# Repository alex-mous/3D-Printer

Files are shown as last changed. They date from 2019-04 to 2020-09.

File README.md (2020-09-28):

<h2> New 3D Printer </h2>

<h3> Introduction </h3>
<h4> Background </h4>
In 2016, I built an Anet A8 budget 3D printer from a kit. During two years of use, the following
issues became evident: <br>
• Print quality (surface quality and amount of ringing) rapidly degraded with an increase in
print speed <br>
• A lack in frame sturdiness caused low quality parts from shaking
induced by the moving axes <br>
• Bolts loosened with use causing rapid degradation in calibration,
giving rise to repeated long setup times <br>
• The heat bed was underpowered and could not heat up quickly or
reach temperatures above 95℃ (required to print certain plastics) <br>
• Print volume was limited to 220x220x230mm

<h4> Engineering Goal </h4>
The goal of this project is to design and build and improved, easy to run, budget 3D printer costing less than $750 for home users to create high quality, high speed prints with a minimum print volume of 275x275x325mm (2.475x10<sup>7</sup>mm<sup>3</sup>).

<h4> Criteria and Constraints </h4>
• Parts and materials must cost less than $750 <br>
• At a print speed of 60mm/s, ringing must be less than a 3 on a ringing scale of 1-6 (1 is negligible, 6 is significant) and roughness must be less than a 3 on a roughness scale of 1-6 (1 is smooth, 6 is rough) <br>
• Print tolerance of ±0.2mm on a 25mm cube <br>
• A minimum print volume of 275x275x325mm (2.475x107mm3) <br>
• Sturdy frame and design <br>
• Powerful heat bed capable of quickly heating to more than 110℃ <br>

<h4> Test Plan </h4>
The following tests were printed on both the Anet A8 and the new printer. The test prints were
then compared and analyzed. <br>
1. Calibration cubes (25x25x25mm) at print speeds from 30-80mm/s in 10mm/s steps with an
acceleration of 1250mm/s2 testing for: <br>
&nbsp&nbsp&nbsp&nbspa. Ringing <br>
&nbsp&nbsp&nbsp&nbspb. Surface quality <br>
&nbsp&nbsp&nbsp&nbspc. Tolerance <br>
2. #3DBenchys to test the ability to print difficult features (such as overhangs, bridges, complex
rounded shapes, etc.) <br>
3. Paper Basket Torture Tests to verify the maximum practical print volumes and identify any
additional common printing issues  <br>

<h4> Results/Conclusion </h4>
<table>
  <tr> <th>Critera and Constraints</th> <th>Result</th> </tr>
  <tr> <td>Parts and materials must cost less than $750</td> <td>✓</td> </tr>
  <tr> <td>At a print speed of 60mm/s, ringing must be less than a 3 on a
ringing scale of 1-6 (1 is negligible, 6 is significant) and roughness
must be less than a 3 on a roughness scale of 1-6 (1 is smooth, 6
is rough)</td> <td>✓</td> </tr>
  <tr> <td>Print tolerance of ±0.2mm on a 25mm cube</td> <td>✓</td> </tr>
  <tr> <td>A minimum print volume of 275x275x325mm (2.475x10<sup>7</sup>mm<sup>3</sup>)</td> <td>4% less than
theoretical due to V3 of Hotend Carriage</td> </tr>
  <tr> <td>Sturdy frame and design</td> <td>✓</td> </tr>
  <tr> <td>Powerful heat bed capable of quickly heating to more than 110℃</td> <td>✓</td></tr>
</table>

<h3>
Warning! This project involves AC wiring and temperatures in excess of 200&degC. Proceed only if you are sure that you know what you are doing!
</h3>

<h3> BOM and Cost </h3>
See BOM.pdf for a list of the parts that need to be purchased. The total cost is around $725. However, your actual cost may vary depending on shipping, tax, etc. Note: the two rolls of PLA filament quoted are an estimate of how much plastic was used. You may find that you need more filament. Also, while you may be able to find cheaper alternatives to some of these parts, please be careful when economizing on very important parts such as the hotend. Some parts may need modification to work properly.

<h3> Tools </h3>
A list of the tooling required is in Tooling.pdf. Please tell me if you find you need more tools so I can add those tools to the list.

<h3> 3D Printed Parts </h3>
The STL files for the 3D printed parts are in the STL files folder. See Printed Parts.pdf for the amount of each part that needs to be printed. Note: some designs may need small modifications after printing such as enlarging holes. Some of these modifications are listed in the Printed Part.pdf file. Please notify me of any modifications made to the parts so that I can update the design files.

<h3> Assembly </h3>
<h4> Step 1: Aluminum Frame </h4>
First, print some of the M6 spacers (see Printed Parts.pdf). Next, prepare an aluminum L-bracket as shown below with two T-slot nuts, two M6x20 screws and two spacers. Repeat this for 28 of the L-brackets.

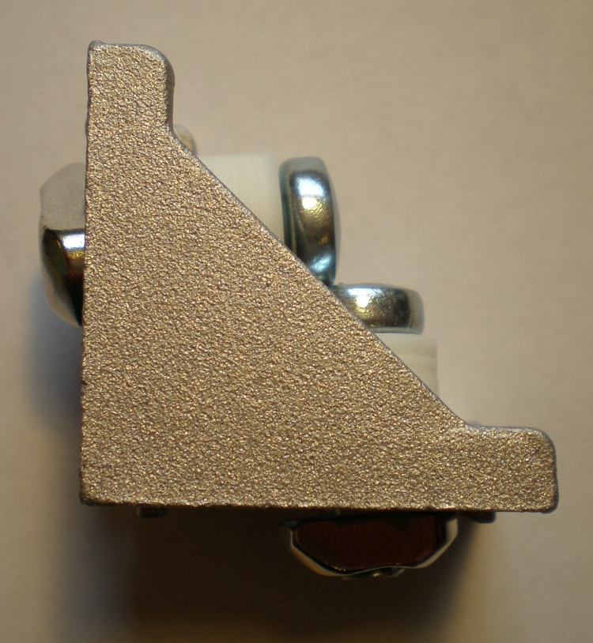
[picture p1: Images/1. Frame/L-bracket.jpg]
Side of bracket
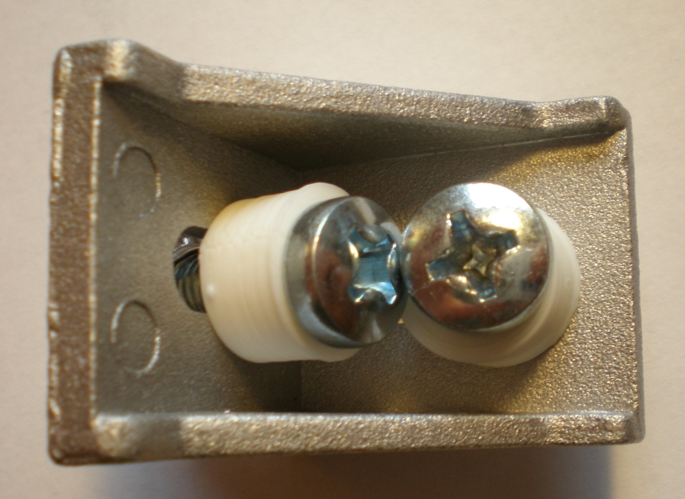
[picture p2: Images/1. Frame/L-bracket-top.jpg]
Top of bracket


<br>

Lay out four of the 470mm lengths of aluminum extrusion; this will create the bottom. Place an aluminum L-bracket at each intersection and start to tighten the screws. Use a square to make sure the frame is square. Repeat these steps for the top (using the remaining four 470mm extrusions). Next, attach the 440mm extrusions at the four corners of the bottom frame using two angle brackets. Use the square to check that the frame is still square. Finally, place the top on top of the 440mm extrusions and attach using the same method as the bottom. Tighten the screws fully while checking the entire frame for squareness. 

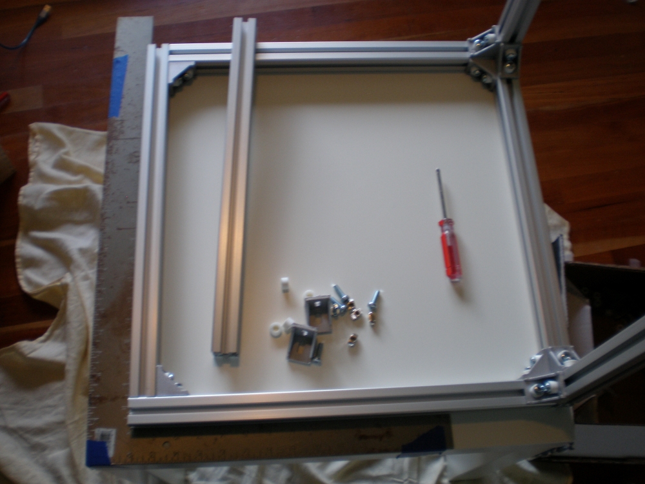
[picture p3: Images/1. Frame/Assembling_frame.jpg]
Partially assembled frame
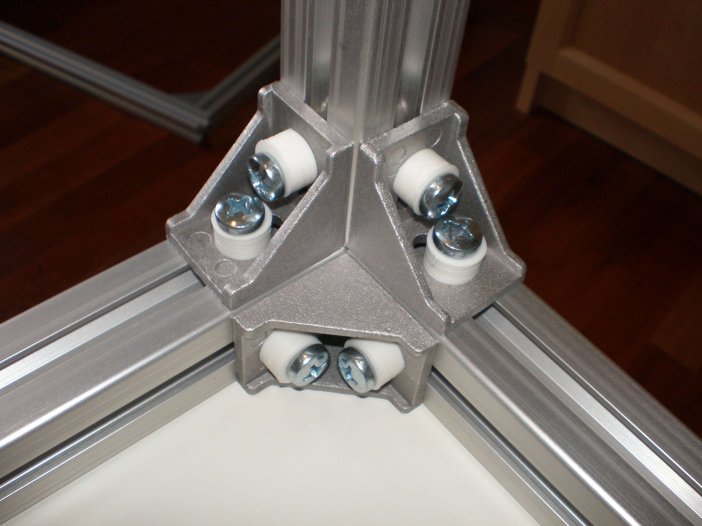
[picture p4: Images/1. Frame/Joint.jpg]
Three-way joint
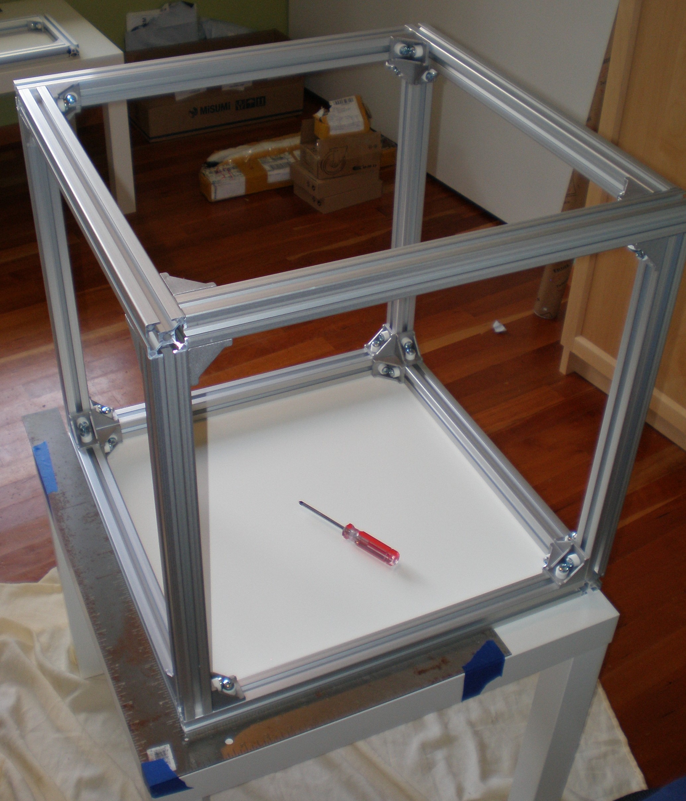
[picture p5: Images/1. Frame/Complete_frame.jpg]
Assembled frame


<h4> Step 2: IKEA Lack Tables </h4>

<h6> Note: drywall screws refers to the 1 1/2" screws unless otherwise noted. </h6>

Print all of the files in the Parts for IKEA Lack tables folder in the STL files folder as directed in Printed Parts.pdf. Attach the four type 1 Mounting/Strengthening Brackets to the bottom of the lower table. Next, place the upper table on top of the lower table and use four of the type 2 brackets to attach them together. Finally, attach the remaining four type 2 brackets to the underside of the upper table. To attach the casters, first push the caster adaptor onto the table leg. Next screw in the two drywall screws on the side. Finally, place the caster on top of the adaptor and screw in four of the 2" drywall screws.

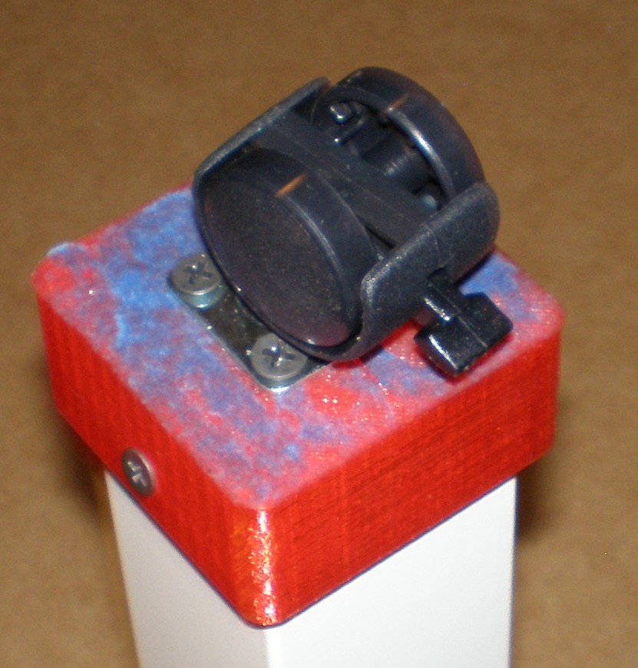
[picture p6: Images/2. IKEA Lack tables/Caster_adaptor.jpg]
Caster adaptor
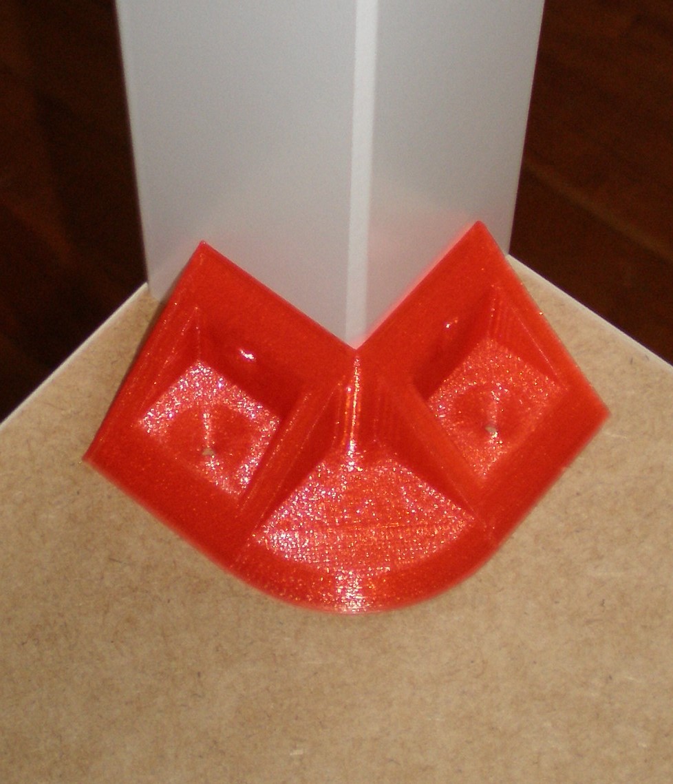
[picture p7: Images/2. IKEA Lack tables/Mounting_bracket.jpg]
Table mounting/strengthening bracket
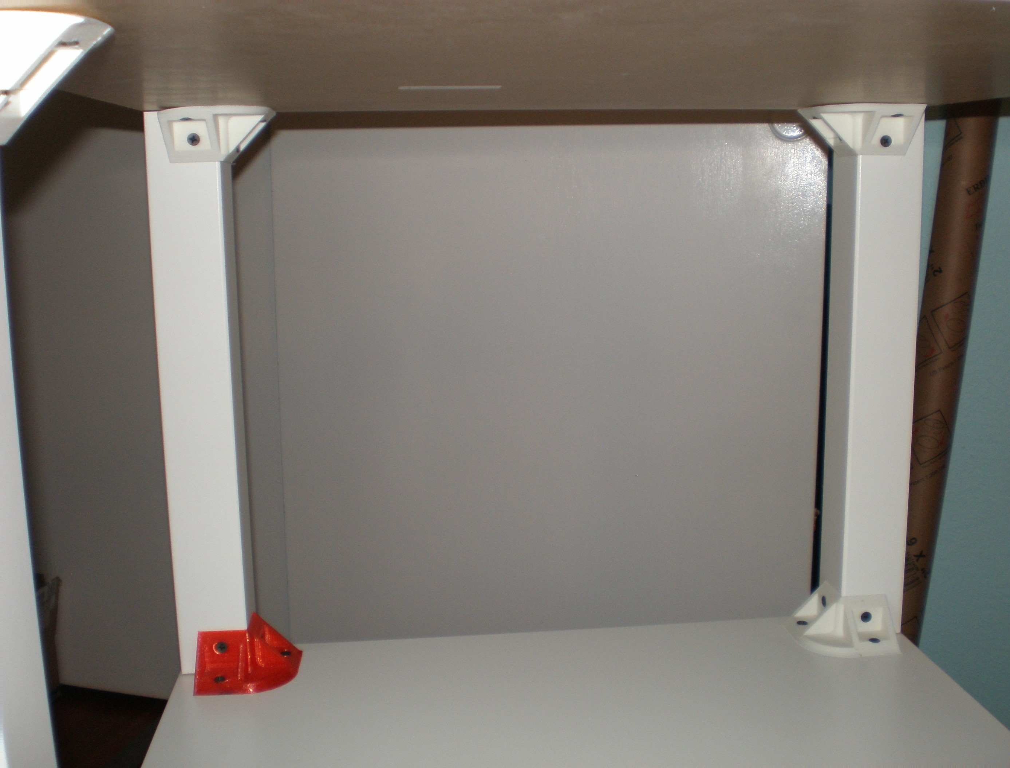
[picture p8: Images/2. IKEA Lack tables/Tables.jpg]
Assembled Tables


Next, attach the main electronics (power supply, SSR, and Arduino/RAMPS combination) to the underside of the top table. Place the electronics as shown below and screw down using drywall screws. (I will cover the wiring later. You may notice that the power wires are soldered to the RAMPS board. That is because the RAMPS board I recieved did not come with an input jack. If your RAMPS also does not come with an input jack, either find an input jack or modify the RAMPS board as I did.)

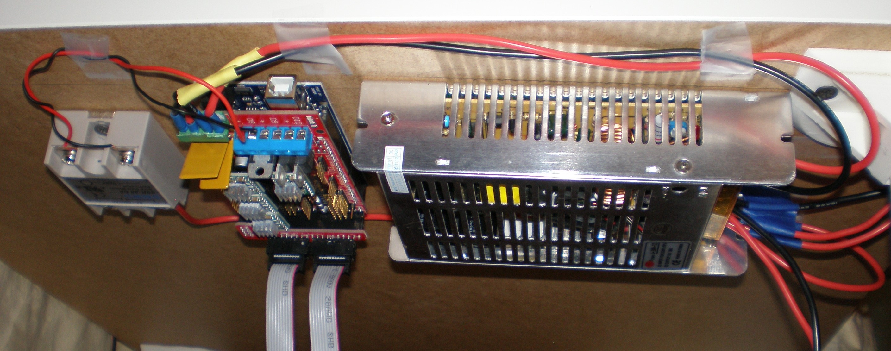
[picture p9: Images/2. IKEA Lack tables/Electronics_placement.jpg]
Electronics placement
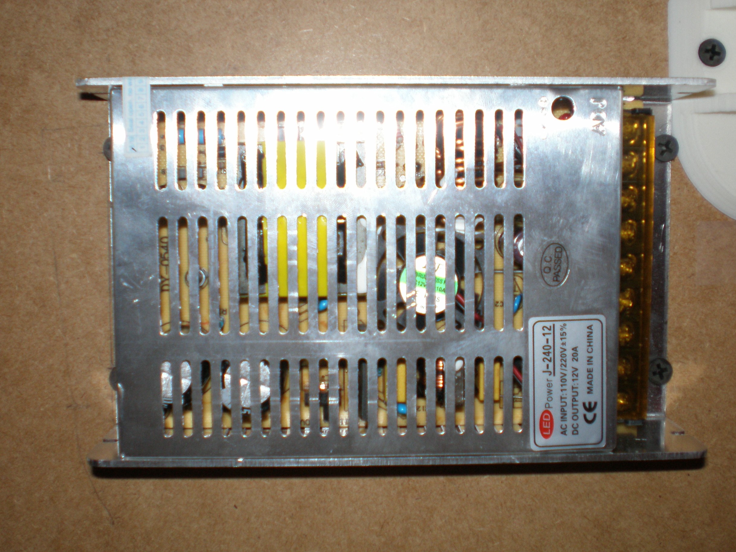
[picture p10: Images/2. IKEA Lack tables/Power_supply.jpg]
Power Supply


For the filament storage, two PVC pipes are clamped on the sides of the upper IKEA Lack table with PVC Pipe Clamps and the remaining two pipes are clamped perpendicular to the sides with PVC Pipes Joiners. To install the PVC Pipe Clamps, carefully measure and mark half-way between the top and the bottom of the upper table on all four table legs. Next, using the square, create a line that passes through the marks on the legs. Place the PVC Pipe Clamp on the leg and mark where the holes should go. Finally, drill the holes and screw the PVC Pipe Clamps on. Slide a PVC pipe through one of the PVC Pipe Clamp, two of thw PVC Pipes Joiners and finally through the another PVC Pipe Clamp.

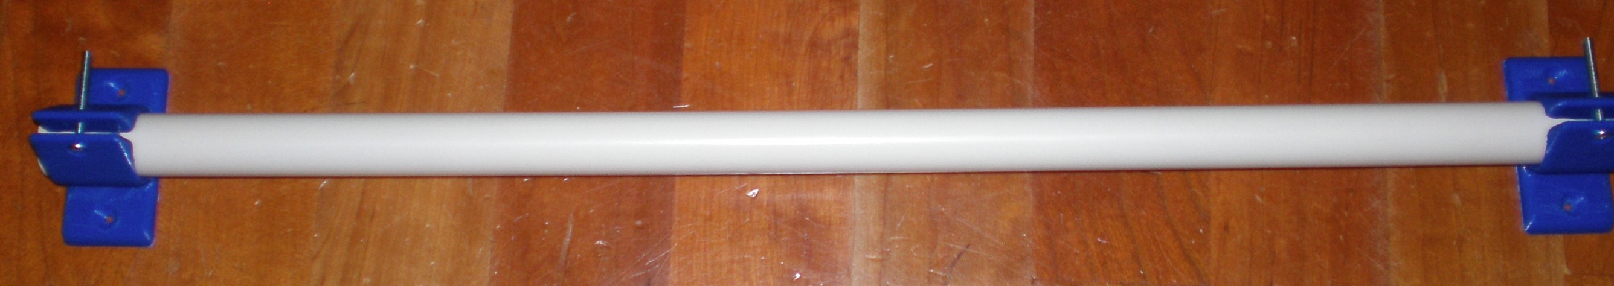
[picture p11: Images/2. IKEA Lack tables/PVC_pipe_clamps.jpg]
PVC Pipe Clamps test fit onto PVC pipe


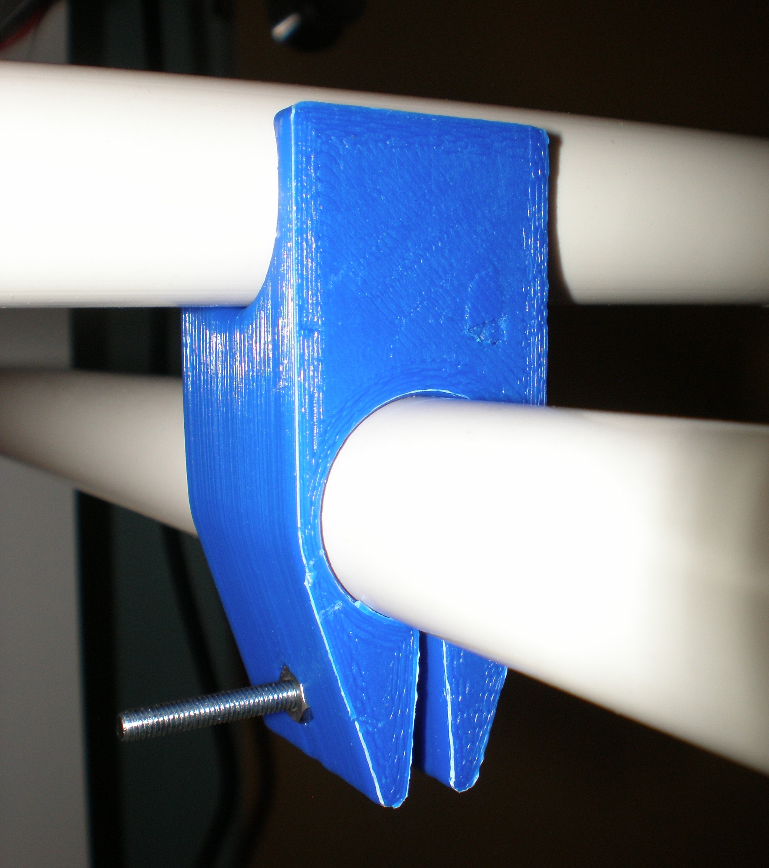
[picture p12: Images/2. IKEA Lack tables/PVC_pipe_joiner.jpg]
PVC pipes joiner
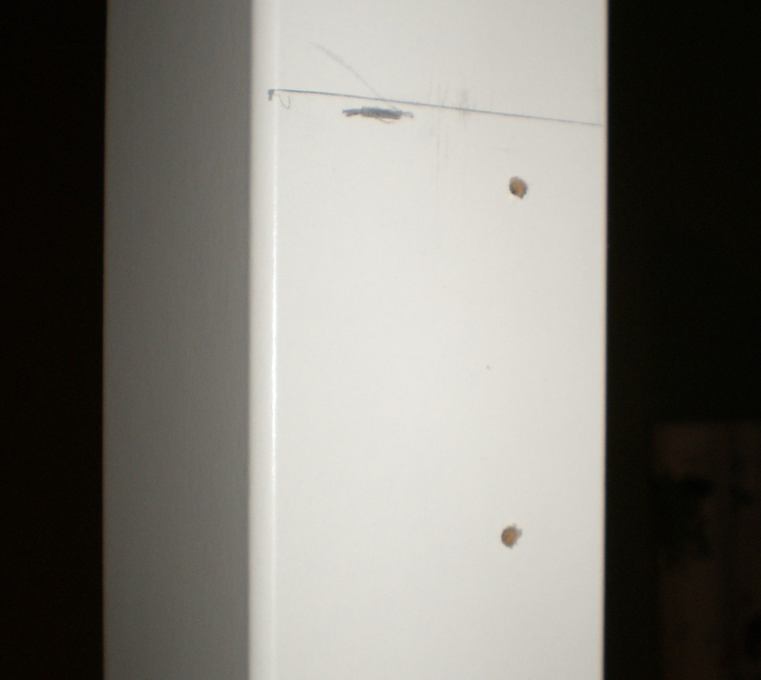
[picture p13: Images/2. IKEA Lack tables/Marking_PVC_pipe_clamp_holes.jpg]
Mark the place where the PVC Pipe Clamps go
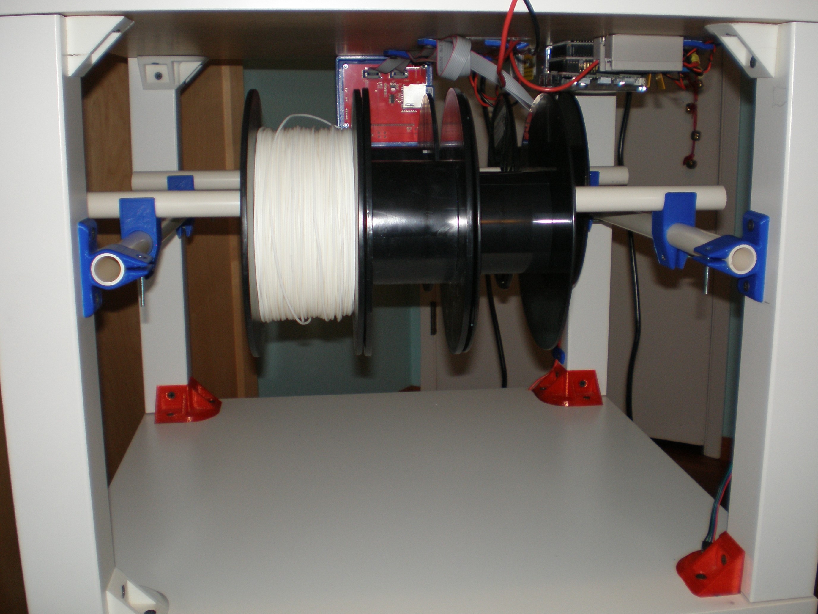
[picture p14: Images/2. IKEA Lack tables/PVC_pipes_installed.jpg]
Fully installed PVC Pipes


<h4> The next two steps involve using TAP Acrylic Cement, which contains a chemical that is suspected of causing cancer. Follow all precautions labelled on the can or use a different adhesive. </h4>
Next, the acrylic hinges need to be attached to two spacers each, drilled with two holes for the coarse thread screws, and attached to the acrylic door panels (the panels on the front and the back of the printer). Also, door knobs need to be attached to the door panels. First, use a saw to cut six 10x25 mm pieces from the 10x10cm acrylic spacer panel. Next, place a spacer on one side of a hinge, making sure that the spacer does not interfere with the joint. Add a drop of acrylic cement to the crack between the hinge and the spacer (the acrylic cement should be automatically spread out inside the crack with capillary action). Repeat these steps for five more acrylic hinges (for a total of six hinges with spacers). Next, drill two holes in each hinge (I recommend stepping up the sizes of drill bits one by one).

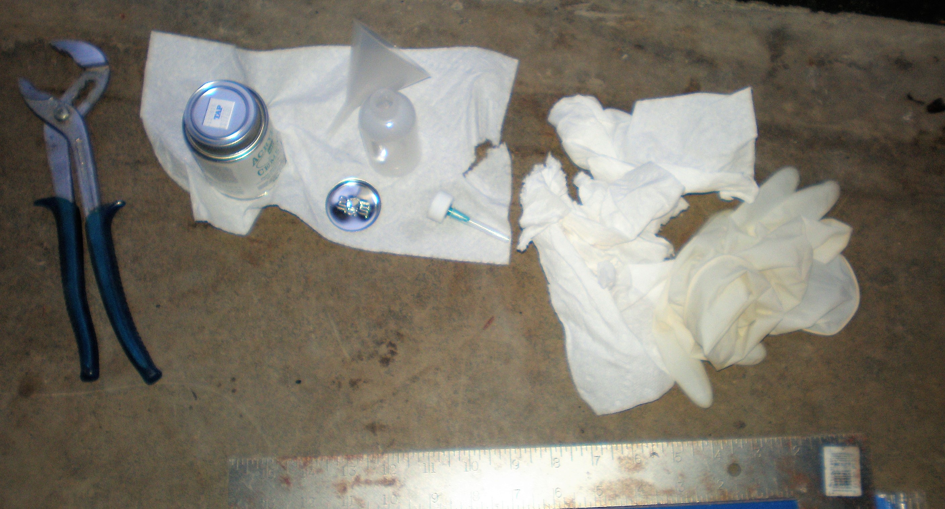
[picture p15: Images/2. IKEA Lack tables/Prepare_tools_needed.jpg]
Prepare tools needed


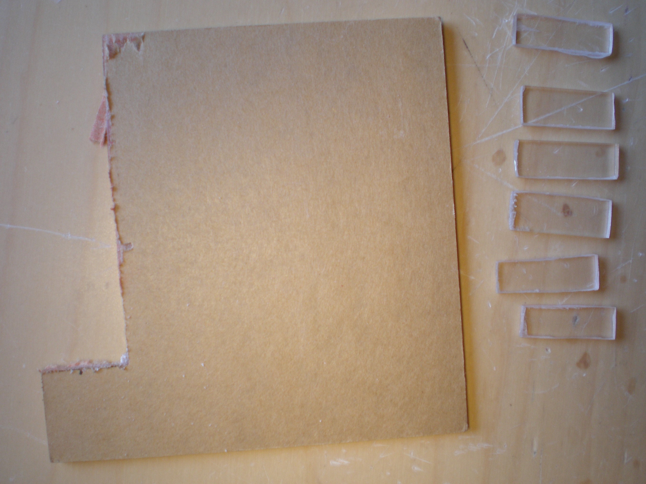
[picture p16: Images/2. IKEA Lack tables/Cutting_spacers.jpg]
Cutting out the 10x25mm spacers
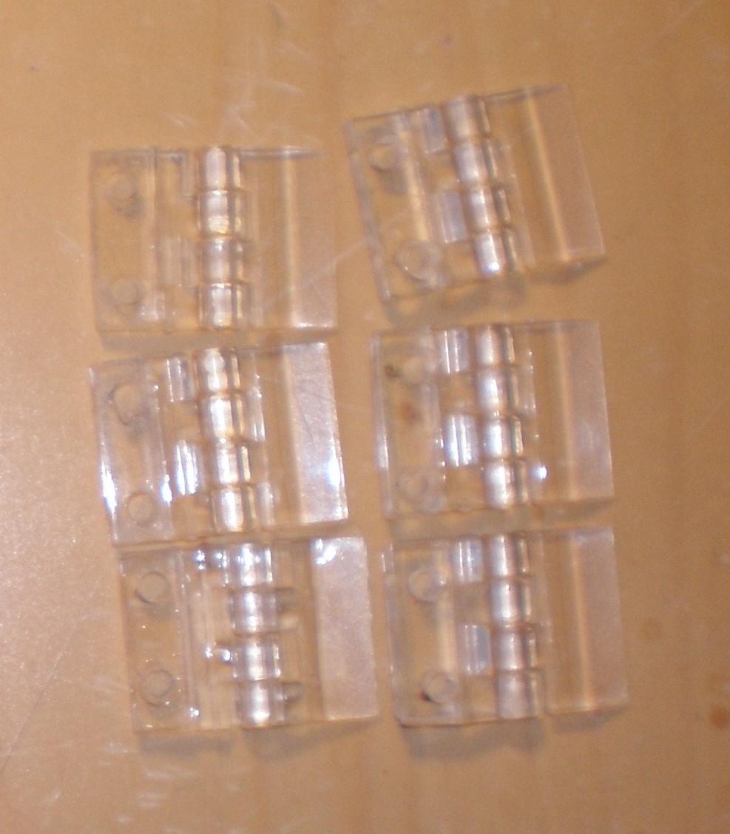
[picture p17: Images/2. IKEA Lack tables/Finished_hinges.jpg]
Finished hinges with spacers attached and holes drilled


The finished hinges and door knobs can now be attached to the main door panels. First, mark out where the hinges and door knob are going to go on one panel. Space the hinges equidistant from each other on one side of the panel (the side of the hinge without the spacer should be on the panel, and the side with the spacer should be off the panel). As before, check that the hinges are placed far enough away from the edge of the panel so the edge does not interfere with the movement of the hinge. The knob can be placed halfway up the panel on the other side of the panel and around x cm in. Using the square to make sure the hinges and knob are aligned, apply acrylic cement as before. Repeat for the second panel.

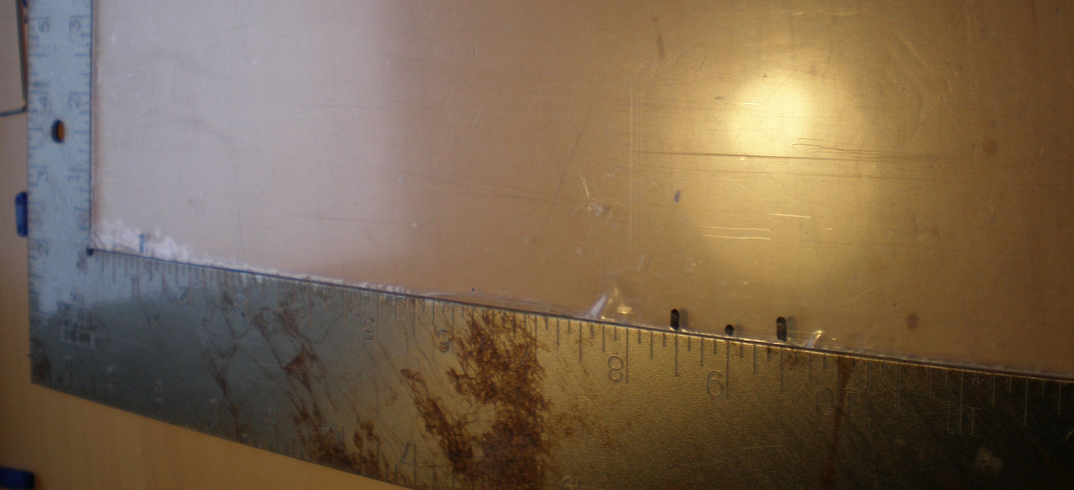
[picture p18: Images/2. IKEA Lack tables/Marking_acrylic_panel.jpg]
Mark out where the hinges and knob should go on an acrylic panel


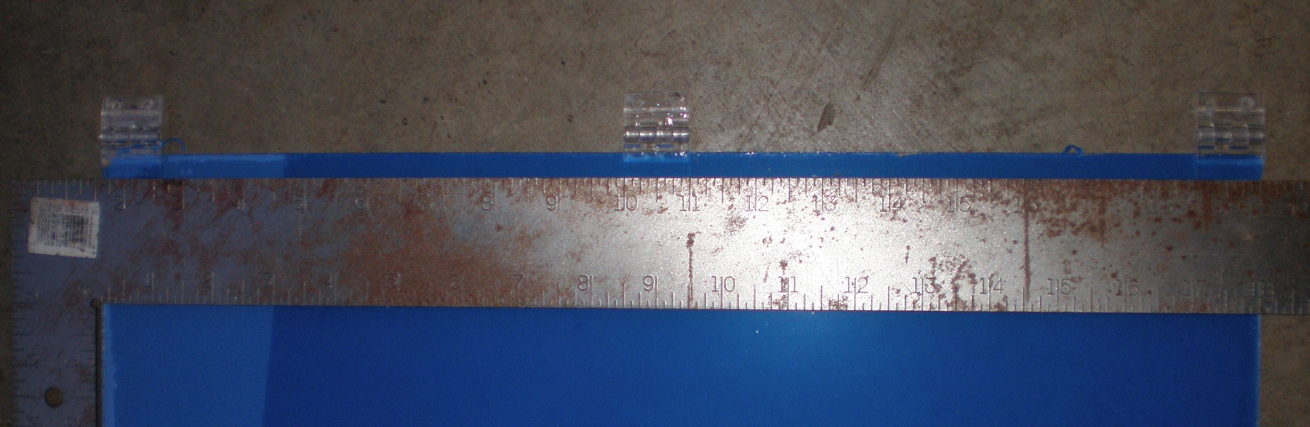
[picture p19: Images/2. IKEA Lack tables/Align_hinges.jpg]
Align the hinges on an acrylic panel
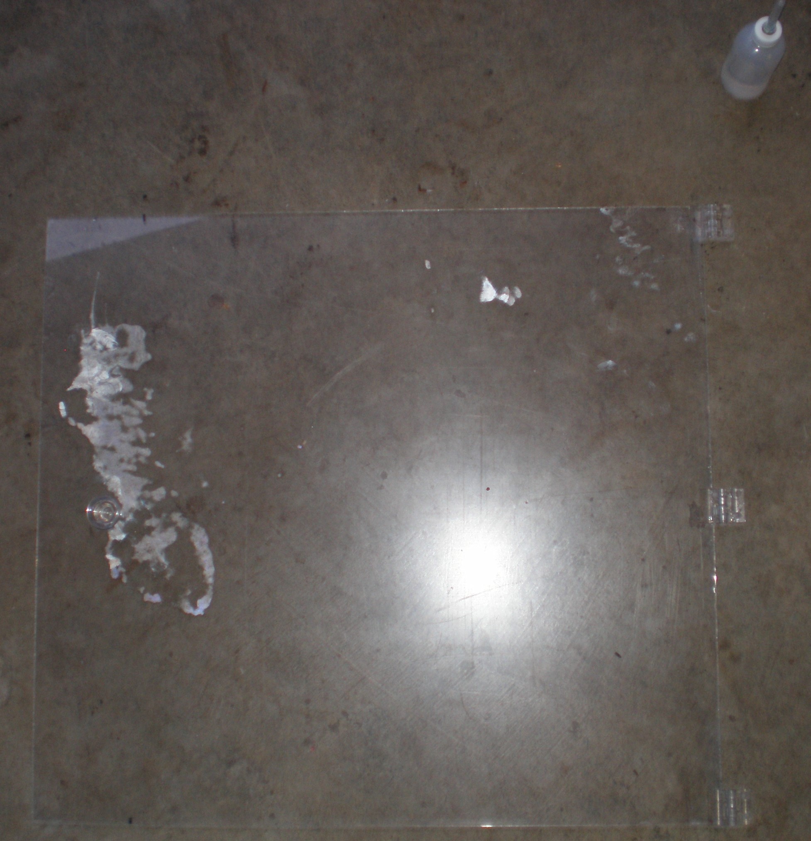
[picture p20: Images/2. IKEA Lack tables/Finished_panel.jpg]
Finished acrylic panel


Before attaching the acrylic panels to the IKEA Lack table, the seal strip should be applied. Peel back the plastic layer on the back of the strip to expose the adhesive. Apply the seal strip as shown in the picture below. (Cut the strip with a box-cutter or scissors.)

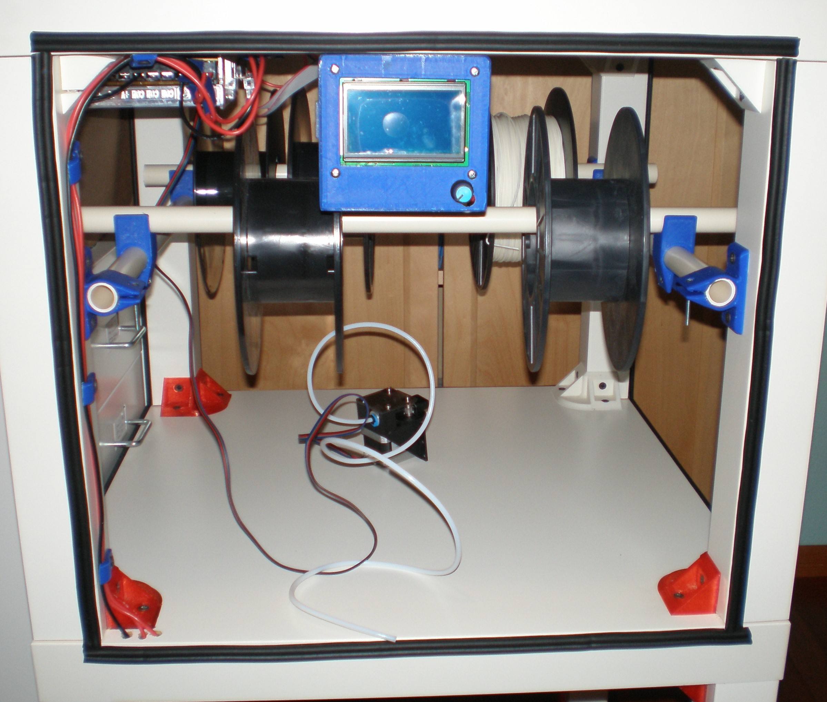
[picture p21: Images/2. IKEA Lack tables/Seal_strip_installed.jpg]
Seal strip installed


Holding a finished acrylic panel up to the front (or back) of the IKEA Lack table, mark out where the holes for the screws should go. Next, drill pilot holes. While holding the panel up, screw the screws in most of the way. (You may want to add a foam spacer to adjust the tension on the hinges from the seal strip.) Fine tune the depth the screws are screwed in to maximize the seal and minimize stress on the acrylic panel. Repeat for the second panel.

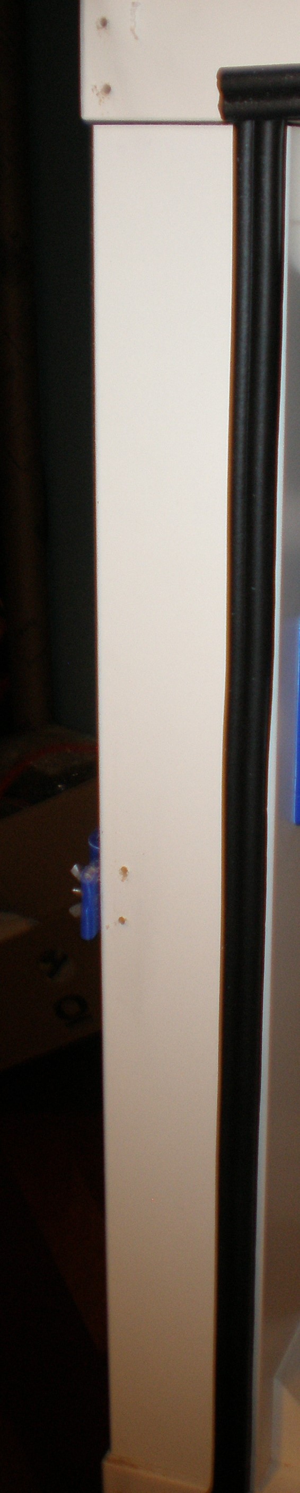
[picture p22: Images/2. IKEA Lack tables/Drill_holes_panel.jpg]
Drilling the holes for an acrylic panel
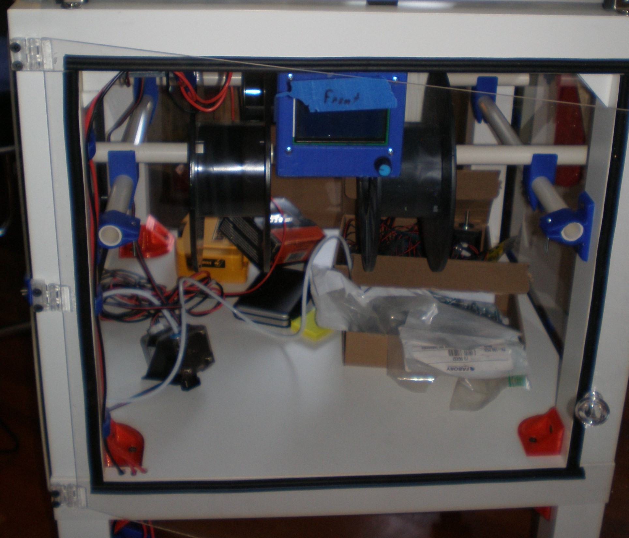
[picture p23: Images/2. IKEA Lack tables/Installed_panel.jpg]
Installed acrylic panel


Now it is time to attach the toggle clamps and panel clamps to secure the acrylic panels. First print out the parts for the Acrylic Toggle Clamps and Acrylic Panel Clamps as directed in Printed Parts.pdf. The toggle clamps must be assembled before they are installed. Follow the steps demonstrated in the pictures to assemble the 10 total clamps. Install the toggle clamps as shown in the picture below by first marking out the locations with a pencil and the square, drilling pilot holes, and screwing in the screws (the edge of the clamp should be flush with the surface of the IKEA Lack table, but check for interference before drilling holes). The Acrylic Panel Clamps do not require assembly, but the installation is a bit trickier. Using the square and the acrylic panel and clamps for reference on the size, mark out where the panel clamps should go (see the picture below, and as before check for interference before installing). To install the set screws, drill pilot holes of 2.5mm. Now screw in the set screws. I found that the hex head on the set screw stripped immediately, so I used two nuts tightened together (as detailed in the picture below) to screw them in. See the picture below for what the finished installation should look like.

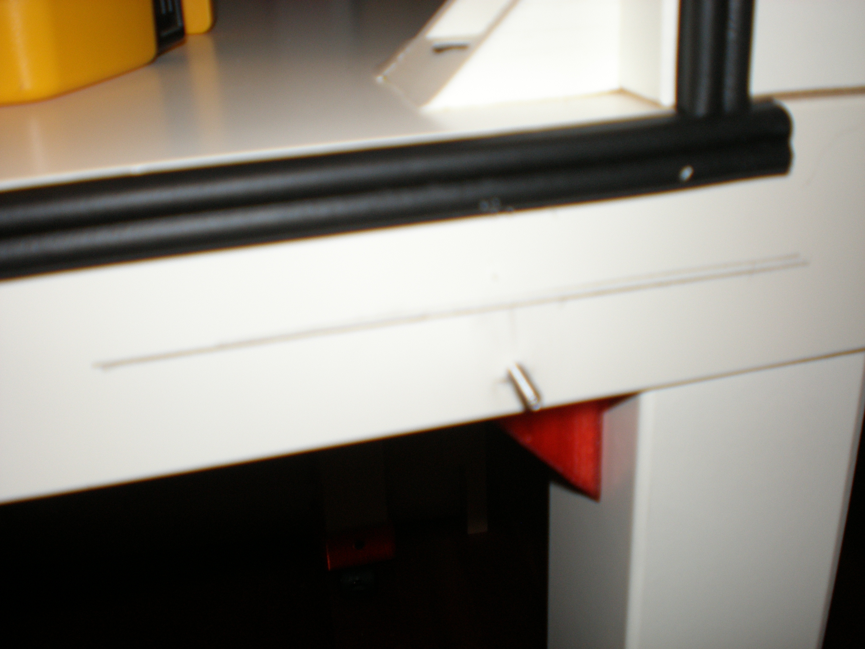
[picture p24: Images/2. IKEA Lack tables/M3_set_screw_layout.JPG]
Layout for the Acrylic Panel Clamps
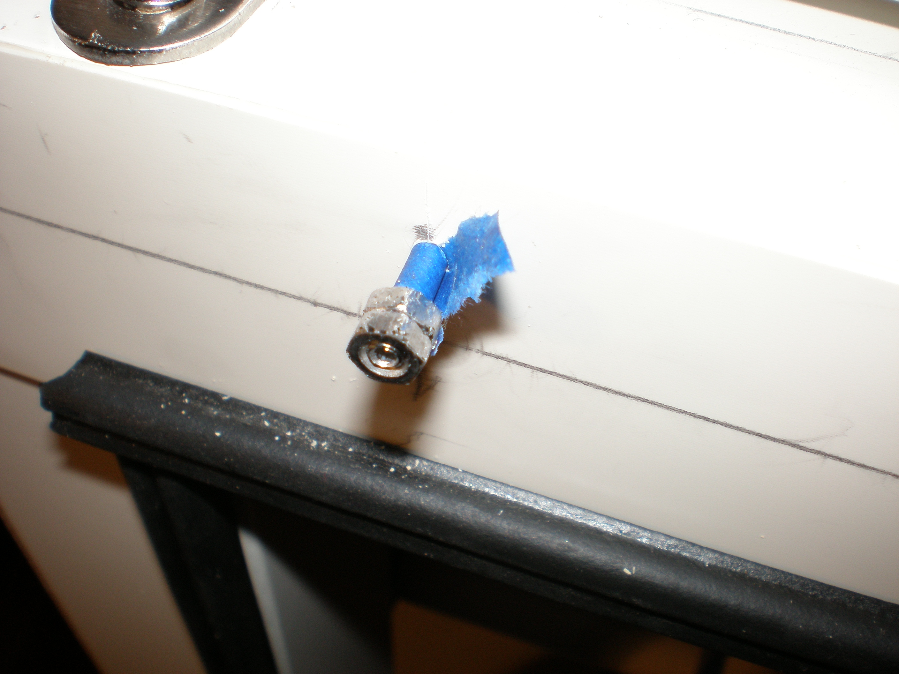
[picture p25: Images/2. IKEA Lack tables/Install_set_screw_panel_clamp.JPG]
Installing set screw
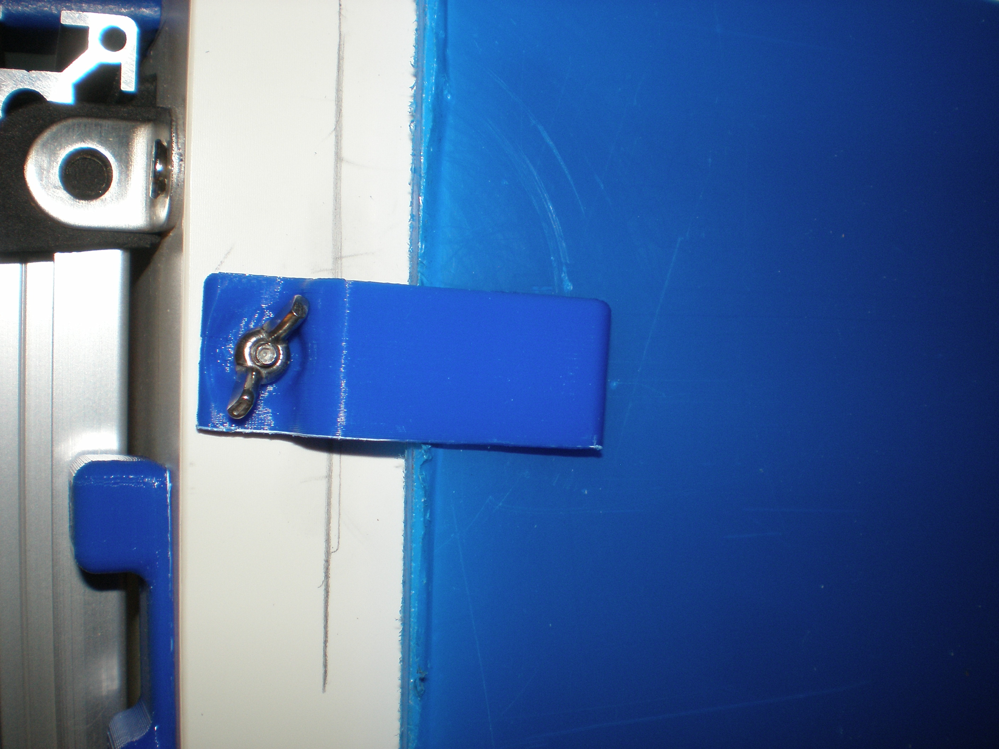
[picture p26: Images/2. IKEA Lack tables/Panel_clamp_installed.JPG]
Installed set screw with panel clamp
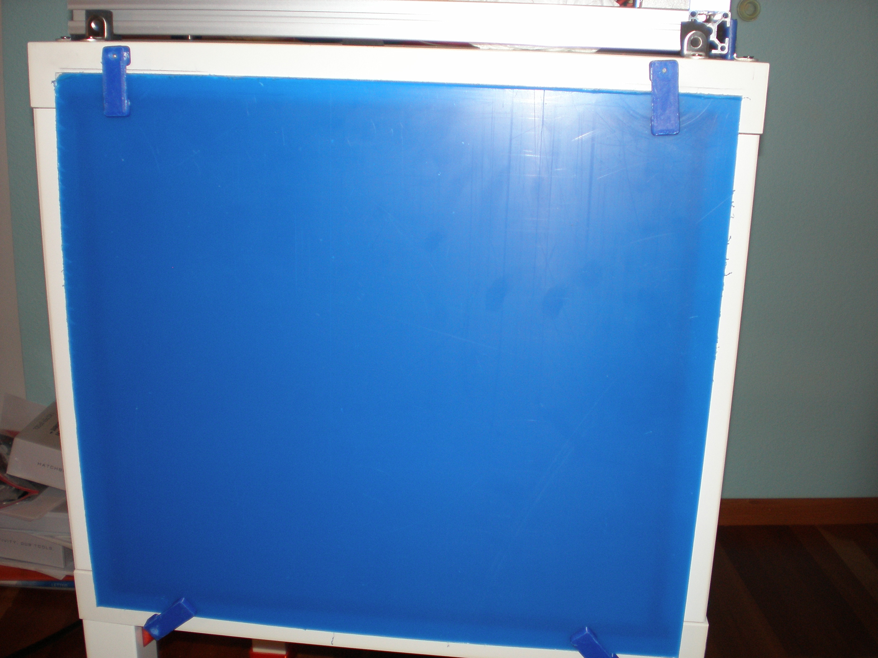
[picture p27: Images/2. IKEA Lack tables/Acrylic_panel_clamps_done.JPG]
Finished


(to be added)

- Attach Printer to top table

<h4> Step 3: Print Bed </h4>
(to be added)

- Create
- Install parts
- Bed supporting plate

<h4> Step 4: Z axis </h4>
(to be added)

- Print parts
- Add 10mm rods
- Bearings to bed supporting plate
- Z leadscrew and nut + parts
- Endstop and adjustable screw (cover software routine)

<h4> Step 5: Y axis </h4>
(to be added)

- Print parts
- Motor Mount
- Idler Bearing Mount
- 12mm Rod Clamp type 1 and 2
- Y endstop
- Motors

<h4> Step 6: X axis </h4>
(to be added)

- Print parts
- aluminum rods and bushings
- Hotend carriage
- XY Joiner
- GT2 Belts
- Hotend install and fan install

<h3> Wiring </h3>
Line up the pins of the RAMPS 1.4 board with the sockets on the Arduino Mega (after the Arduino Mega is fully screwed down onto the IKEA Lack table). Press the RAMPS 1.4 board down until the pins are fully into the Arduino Mega. Next, solder wires to the switch as shown below in the pictures. Follow the wiring diagram below (this diagram is in SVG format and can therefore be scaled) (Note: some wires/cables will need to be extended. You can splice four wires into multi-core cable listed in the BOM instead of using seperate pieces of wire (see pictures below for an example)). Add 3D-printed wire clamps (see the STL files folder and Printed Parts.pdf), zip-ties and labels as necessary. Below the wiring diagram are some pictures of the wiring.

<h4> Wiring Diagram </h4>
Wiring schematic SVG

<h4> Switch wiring </h4>

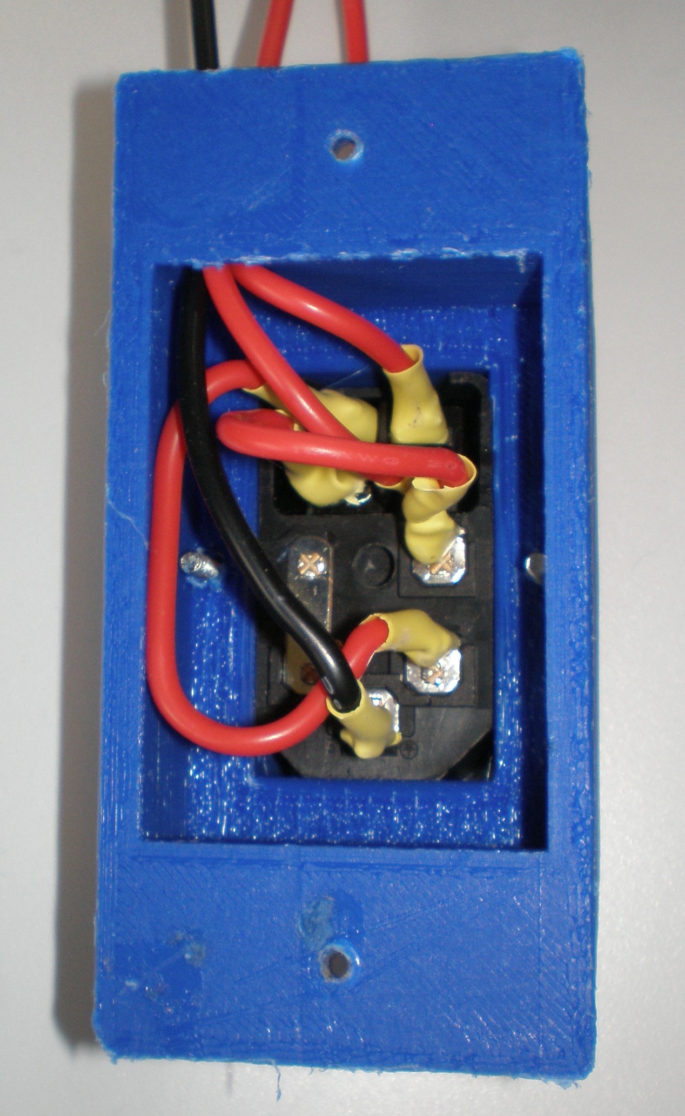
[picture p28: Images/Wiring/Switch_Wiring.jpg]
Switch wiring back
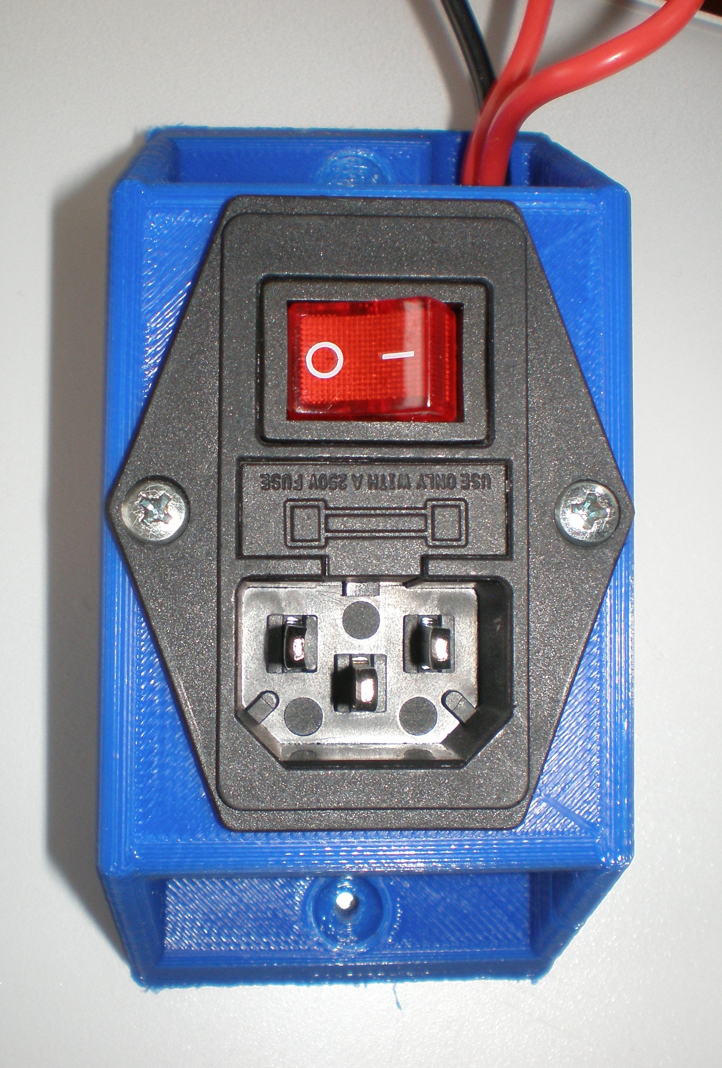
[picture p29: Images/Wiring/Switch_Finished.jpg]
Switch wiring front JPG


<h4> Multi-core Cable spliced to Endstop wires </h4>

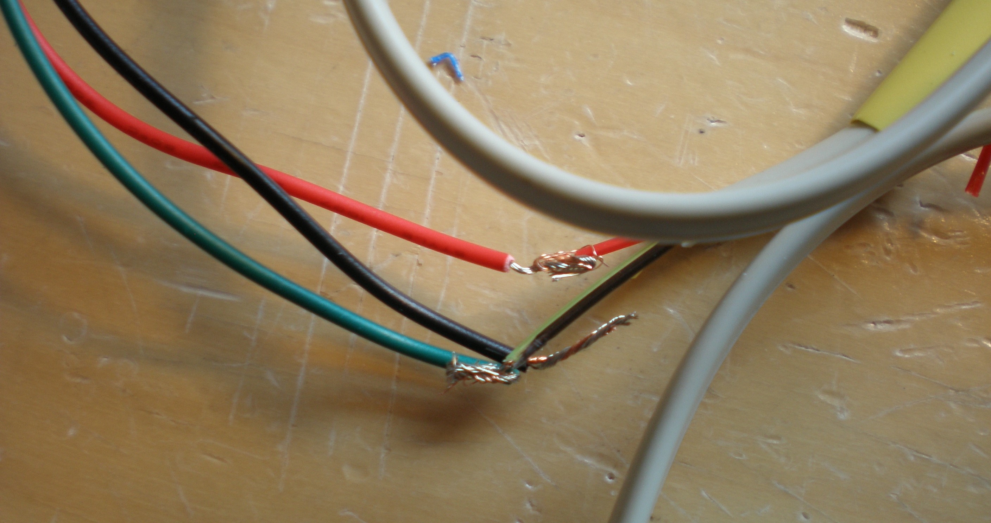
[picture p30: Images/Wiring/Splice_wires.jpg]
Splicing wires to cable
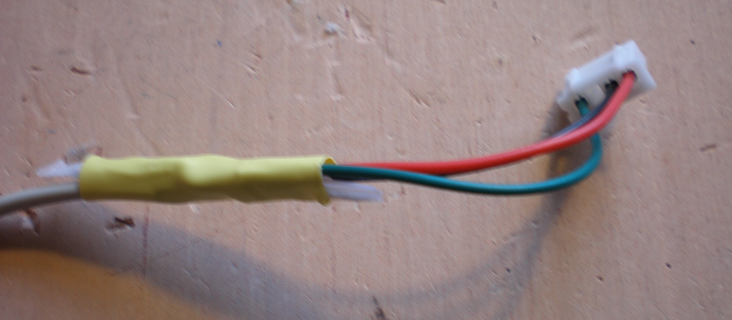
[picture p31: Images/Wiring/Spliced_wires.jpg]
Spliced wires to cable


<h4> Starting Wiring </h4>

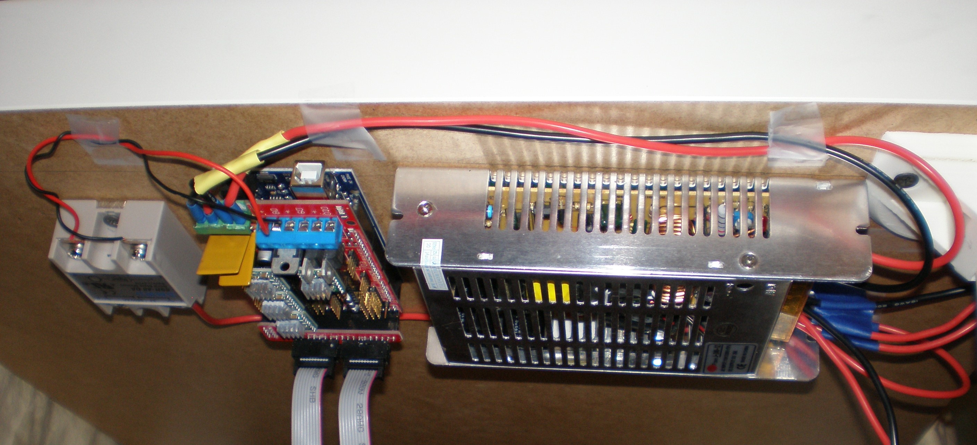
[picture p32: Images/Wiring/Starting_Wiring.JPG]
Starting wiring


<h4> Finished Wiring </h4>

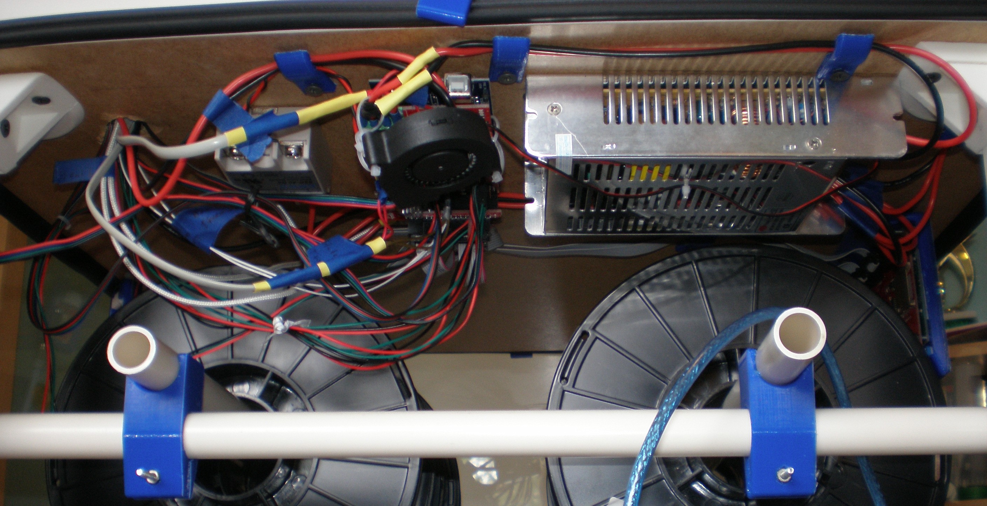
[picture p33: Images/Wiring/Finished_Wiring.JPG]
Finished wiring


<h3> Firmware </h3>
Marlin firmware is used for this 3D printer(see <a href="https://marlinfw.org">marlinfw.org</a>). The Marlin Configuration folder stores the changed configuration files in Marlin. See MODIFICATIONS.txt for how to install the configuration files and upload Marlin to the Arduino Mega.

<h3> Software </h3>
I recommend using Ultimaker Cura for slicing. Cura can be installed from <a href="https://www.ultimaker.com/en/products/ultimaker-cura-software">the Ultimaker website</a>. A sample profile is the main directory. Follow the instructions detailed on <a href="https://www.ultimaker.com/en/resources/20441-manage-profiles">this page on the Ultimaker website</a> to load the profile. To perform one of the test prints: load the test cube from the STL files folder into Cura, slice the cube, and put the GCODE on an SD card. Insert the SD card into the 3D printers LCD sreen controller board and select the file from the menu.

<h3> License and Credits </h3>
All work is licensed under the Creative Commons Attribution-ShareAlike 4.0 International license, except for the Marlin configuration files. Note: the Marlin configuration files (Configuration.h, Configuration_adv.h, pins_RAMPS.h, ultralcd.cpp) are licensed differently because they are from Marlin (see <a href="https://marlinfw.org">marlinfw.org</a>). For those files, see the LICENSE in the Marlin Configuration directory. This design was inspired by Tech2C's Hypercube, but all of the parts and components, from major axis design and structure to motor and wiring placement, were designed by me from scratch.

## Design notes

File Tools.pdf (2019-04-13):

Tools

## Tooling Used

Tool Name | Function
3D Printer (Anet A8) | Printing parts
Box-cutter | Stripping small wires and cutting other items such as paint off of Lack tables
Calipers | Measuring accuracy of printed parts and creating drawings
Center Punch | Creating guide hole in jig and tool plate before drilling
Clamps (Bar, Spring, etc.) | Securing parts while cutting and assembling
Computer and peripherals | Creating designs and researching processes
Dril | Drilling holes in Lack table
Drill bits | Used in drill
Drill Press (used off site) | Aluminum bed plate mounting holes
Funnel | Pouring acrylic cement out of can and into applicator
Hacksaw | Cutting metal rods and plastic
Hand drill | Drilling small holes or where power drill would not fit
Heat Gun | Removing stringing from Paper Basket Torture Test
Heat Gun | Shrinking heat shrink tube
Hex wrenches | Hotend and set screws required head
Hot Glue Gun | Temporarily attaching toggle clamps
Many types of screwdrivers | Screwing in screws
Metal hammer | Cleaning up large prints and stress-testing unused parts
Multi-grips | Removing lid from acrylic cement and other
Multimeter | Checking for voltage resistance and continuity
Needle-nose pliers | Cleaning up prints, threading wires, etc.
Nitrile Gloves | Prevent solvent during solvent welding from contacting hands
PanaVise 201 | Holding parts while drilling small holes and cleaning up
Putty Knife | Scraping prints of of bed and cleaning up prints
Respirator Dust Mask | Protect from wood dust
Ruler | Measuring distances where stiff surface was needed
Safety Glasses | Protect from air-born solder and flying owed and plastic particles
Sandpaper | Sanding down rough surfaces on parts and changing size to make parts fit better
Self-closing tweezers | Gripping hard to hole wires and small parts
Skewer | Applying glue to parts
Small wooden hammer | Adjust dimensions/squareness of frame and cleaning up prints
Soldering Iron | Soldering wires
Soldering Tools from Maplin | Cleaning up prints
Solvent Applicator | Solvent welding acrylic
Square | Making frame square
Tap, M3x0.5 | Making holes threaded holes in aluminum bed plate (Irwin plug tap)
Tap Wrench | Turning taps (Irwin tap wrench)
Tape Measure | Measuring distances larger than calipers can span
Thick Gloves | Guard against tools when cleaning up prints
Utility Knife | Removing stringing from Paper Basket Torture Test
Ventilation Fan | Suck out 3d printing and soldering fumes
Wire cutters | Cleaning up prints and cutting wires
Wire Strippers | Cleaning up prints and stripping large wires

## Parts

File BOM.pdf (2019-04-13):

Parts and Materials Purchased

## Parts and Materials Purchased

Qty of Lots | Part Description, Dimensions and Selection | Cost | Supplier | Link | .
1 | Linear Shafts 10mm OD 500mm L (pack of 2) | $15.20 | Aliexpress | | . (https://www.aliexpress.com/store/product/2pcs-8mm-8x400-linear-shaft-3d-printer-8mm-x-400mm-Cylinder-Liner-Rail-Linear-Shaft-axis/1762258_32332798910.html)
1 | Linear Shafts 12mm OD 500mm L (pack of 2) | $19.10 | Aliexpress | | . (https://www.aliexpress.com/store/product/2pcs-8mm-8x400-linear-shaft-3d-printer-8mm-x-400mm-Cylinder-Liner-Rail-Linear-Shaft-axis/1762258_32332798910.html)
1 | Linear Bearings LM10LUU (pack of 4) | $8.28 | Aliexpress | | . (https://www.aliexpress.com/store/product/4pcs-lot-Free-shipping-LM12UU-Linear-Bushing-12mm-CNC-Linear-Bearings/1762258_32317273540.html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)
1 | Linear Bearings LM12LUU (pack of 4) | $8.91 | Aliexpress | | . (https://www.aliexpress.com/store/product/4pcs-lot-Free-shipping-LM12UU-Linear-Bushing-12mm-CNC-Linear-Bearings/1762258_32317273540.html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)
1 | Anti-Backlash Nut Tr8x8x2 (pack of 2) | $7.64 | Aliexpress | | . (https://www.aliexpress.com/store/product/2pcs-TR8x8-TR8x4-TR8x2-8mm-Acme-Anti-Backlash-Nut-Block-for-CNC-3D-printer-spare-parts/2412069_32809617055.html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)
1 | Stepper Motor for Z with Lead Screw 500mm L | $23.91 | Aliexpress | | . (https://www.aliexpress.com/item/Nema17-17HS4401-stepper-motor-with-T8-screw-lead-8mm-300-400-500mm-42-motor-42BYGH-3D/32888650990.html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)
1 | Nema 17 Stepper Motor 48 Ncm (pack of 3) | $30.66 | Aliexpress | | . (https://www.aliexpress.com/store/product/Free-shipping-3PCS-4-lead-Nema17-Stepper-Motor-42-motor-17HS8401S-1-8A-CE-ROSH-ISO/432672_32819461559.html)
3 | Aluminum 3030 Corner Brackets (pack of 10) | $20.64 | Aliexpress | | . (https://www.aliexpress.com/store/product/HOTSale-10pcs-3030-corner-fitting-angle-aluminum-30-x-30-L-connector-bracket-fastener-match-use/1762258_32640846023.h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)
1 | Locking Caster 30mmx30mm base 15kg load supporting (pack of 4) | $11.14 | Aliexpress | | . (https://www.aliexpress.com/store/product/4PCS-EDL-30mm-15Kg-PA-Nylon-furniture-Castors-Wheels-Plate-Brake-Locking-Small-Furniture-Caster-Wheels/1994013_328304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)
2 | GT2 Idler 20T W6 B3 With T 5 per lot (pack of 5) | $8.47 | Aliexpress | | . (https://www.aliexpress.com/store/product/10pcs-GT2-Idler-Timing-Pulley-16-20-Tooth-Wheel-Bore-3-5mm-Aluminium-Gear-Teeth-Width/432672_32822906447.html)
2 | GT2 Pulley 16 teeth 5mm bore | $1.06 | Aliexpress | | . (https://www.aliexpress.com/store/product/3D-Printer-Parts-Accessory-GT2-16teeth-16-teeth-Bore-5mm-Timing-Alumium-Pulley-fit-for-GT2/432672_32784183624.html)
1 | Anti-Vibration Pads for Table 77x77x7mm LxWxH (pack of 4) | $1.51 | Aliexpress | | . (https://www.aliexpress.com/store/product/New-4pcs-Washing-Machine-Anti-Vibration-Pad-Shock-Proof-Non-Slip-Foot-Feet/2673139_32862401857.html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)
1 | Fiberglass GT2 Belt 5m L | $5.22 | Aliexpress | | . (https://www.aliexpress.com/store/product/5m-lot-GT2-6mm-open-timing-belt-width-6mm-GT2-belt-Rubbr-Fiberglass-cut-to-length/2498059_32811832945.html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)
4 | Table Mounting Brackets (pack of 2) | $3.89 | Aliexpress | | . (https://www.aliexpress.com/item/1PCS-YT784-Thickening-Stainless-Steel-Bracket-Rectangular-L-Fixed-Bracket-Furniture-Fastening-accessories-20-20-16mm/327759297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)
1 | T Slot Nuts M6 m6 100pcs (pack of 100) | $10.66 | Aliexpress | | . (https://www.aliexpress.com/store/product/100pcs-50pcs-3030-Aluminum-Profile-with-Slot-Groove-8mm-M4-M5-M6-Nickel-Plated-T-Bolt/937165_32825325332.html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)
4 | Aluminum Extrusion 3030 Frame 440mm L HFS | $17.60 | Misumi | | . (https://us.misumi-ec.com/vona2/detail/110302686450/?Inch=0&Tab=wysiwyg_area_0)
8 | Aluminum Extrusion 3030 Frame 470mm L HFS | $37.60 | Misumi | | . (https://us.misumi-ec.com/vona2/detail/110302686450/?Inch=0&Tab=wysiwyg_area_0)
4 | Aluminum Extrusion 3030 Bed 280mm L | $17.88 | Misumi | | . (https://us.misumi-ec.com/vona2/detail/110302686450/?Inch=0&Tab=wysiwyg_area_0)
1 | Anodized Aluminum Tubing 3/8”Dx29/200"IDx72""L | $12.14 | McMaster-Carr | | . (https://www.mcmaster.com/4568t12)
2 | LACK Side table 550x550x450mm Feet: ~50x50mm | $29.98 | IKEA | | . (https://www.ikea.com/us/en/catalog/products/60193736/)
1 | M3x25x0.5 for Pulleys (pack of 100) | $8.24 | Gamut | | . (https://www.gamut.com/p/pan-head-machine-screw-steel-zinc-plated-phillips-m3-thread-size-NDAyNTU)
1 | M3x0.5 Nut for Pulley 5.5mm W 2.41mm H (pack of 100) | $0.62 | Gamut | | . (https://www.gamut.com/p/hex-nut-steel-plain-class-8-material-grade-m3-thread-size-ODU4MQ)
1 | M6x20x1.0 for Mounting (pack of 100) | $21.01 | Gamut | | . (https://www.gamut.com/p/pan-head-machine-screw-steel-zinc-plated-phillips-m6-thread-size-NTQxMQ)
1 | M3 Set Screws 25mm L M3X25(50pcs) (pack of 50) | $6.99 | Aliexpress | | . (https://www.aliexpress.com/store/product/Hex-Head-Socket-Cap-Set-Grub-Screw-Hexagon-Metric-Thread-Headless-Allen-head-Cup-Point-Bolt/4042031_32879520575.html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)
1 | Aluminum 3030 2-Hole Connector Plates for Bed 30s 10pcs (pack of 10) | $8.99 | Aliexpress | | . (https://www.aliexpress.com/store/product/Link-End-Parallel-Side-by-Side-Vertical-Joint-Connect-Angle-Connector-Strip-for-2020-20x20-Aluminum/937165_2043798062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)
1 | Silicone Heating Pad 300x300mm 120V 750W | $24.62 | Aliexpress | | . (https://www.aliexpress.com/store/product/DuoWeiSi-3D-Printer-Parts-300x300mm-120V-750W-Silicone-Heater-Pad-For-3D-Printer-Heated-Bed-Heating/2882163_328225421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)
1 | M3 Knurled Thumb Nuts (pack of 10) | $0.99 | Aliexpress | | . (https://www.aliexpress.com/item/10pcs-M3-GB807-Handle-nuts-Knurled-thumb-nuts-hw146017/32756573704.html)
1 | M3 Washers for Thermistor Mount (pack of 50) | $3.36 | Aliexpress | | . (https://www.aliexpress.com/item/M3-M4-M5-M6-M8-M20-Large-Flat-Washer-304-Stainless-Steel-Big-Metal-Gasket-Meson/32847105986.html)
1 | SSR for Silicone Heat Pad SSR 40DA | $5.86 | Aliexpress | | . (https://www.aliexpress.com/item/1pcs-Free-shipping-solid-state-relay-SSR-10DA-10A-actually-3-32V-DC-TO-24-380V/32706812752.html)
1 | 100k NTC Thermistor (pack of 10) | $2.83 | Aliexpress | | . (https://www.aliexpress.com/item/10Pcs-lot-100K-ohm-NTC-3950-Thermistors-for-3D-Printer-Reprap-Mend-Free-Shipping/32639944762.html)
1 | Cast Aluminum Bed 1/4"" H 13"" L 13"" W | $54.48 | Midwest Steel and Aluminum | | . (https://www.midweststeelsupply.com/store/castaluminumplateatp5)
1 | M6x12x1.0mm Screws (pack of 100) | $15.91 | Gamut | | . (https://www.gamut.com/p/pan-head-machine-screw-steel-zinc-plated-phillips-m6-thread-size-MTA4NTk1)
1 | M3 Nylon Spacers For Bed 10mm L 5mm OD (pack of 10) | $1.80 | Gamut | | . (https://www.gamut.com/p/nylon-spacer-metric-black-m3-screw-size-10-mm-overall-lg-MzYyMTY)
1 | M3x4 Screws for Thermistor (pack of 100) | $6.39 | Gamut | | . (https://www.gamut.com/p/pan-head-machine-screw-steel-zinc-plated-phillips-m3-thread-size-ODk1MDI)
1 | M3x10x0.5 for Motors (pack of 25) | $4.89 | Gamut | | . (https://www.gamut.com/p/pan-head-machine-screw-steel-zinc-plated-phillips-m3-thread-size-MTEyOTU)
4 | PVC Pipe 20mm D 50cm L White | $10.79 | Aliexpress | | . (https://www.aliexpress.com/item/Blue-White-PVC-Pipe-OD-20mm-25mm-32mm-Agriculture-Garden-Irrigation-Tube-Fish-Tank-Water-Pipe/32948244693.html)
1 | Power Supply 12V 20A | $15.25 | Aliexpress | | . (https://www.aliexpress.com/item/Hot-Sale-AC85-265V-110V-220V-to-DC5V-12V-24V-36V-48V-1A-2A-3A-5A/32780272089.html)
1 | Switch and C14 Socket 10A fuse Red | $0.93 | Aliexpress | | . (https://www.aliexpress.com/item/Baomain-IEC-320-C14-Red-Light-Rocker-Inlet-Male-Power-Supply-Connector-Plug/32706948395.html)
3 | Boxes of Silica Gel Yellow | $7.25 | Aliexpress | | . (https://www.aliexpress.com/item/Silica-Gel-Box-1pc-Reusable-White-Orange-Blue-Silicagel-Moisture-Absorber-Absorbent-Desiccant-Box-Color-Changing/32793744530.h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)
1 | Arduino Mega RAMPS 1.4, A4988 Stepper Drivers, Endstops, LCD | $36.85 | Aliexpress | | . (https://www.aliexpress.com/store/product/CNC-3D-Printer-Kit-for-Arduino-Mega-2560-R3-RAMPS-1-4-Controller-LCD-12864-6/415445_32685004463.html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)
1 | Silicone Wire Flexible 10m 16AWG half of red black | $12.92 | Aliexpress | | . (https://www.aliexpress.com/item/50Meter-6-7-8-10-11-12-13-14-15-16-17-18-20-22-24/32718990317.html)
1 | Acrylic Offset for Hinges 100x100x3mm A2 | $3.28 | Aliexpress | | . (https://www.aliexpress.com/item/1pcs-Clear-Acrylic-Perspex-Sheet-Cut-Plastic-Transparent-Board-Perspex-Panel-2-5mm-thickness/32850622506.html)
1 | Acrylic Hinges 25 x 33 x 3mm (pack of 10) | $2.42 | Aliexpress | | . (https://www.aliexpress.com/item/10Pcs-Durable-Clear-Acrylic-Plastic-Folding-Hinges-Plexiglass-Hinge/32889707845.html)
1 | Titan Extruder and V6 Hotend and Motor Type 3 | $25.04 | Aliexpress | | . (https://www.aliexpress.com/item/3D-Printer-Parts-DIY-Titan-Extruder-Fully-Kits-With-Nema-17-Stepper-Motor-For-V6-J/32865543307.html)
1 | PTFE Tube and Pneumatic Couplers 2mm ID 4mm OD 1m L Type C | $3.28 | Aliexpress | | . (https://www.aliexpress.com/store/product/Hot-1M-PTFE-Tube-Teflon-PC4-M6-PC4-01-Fitting-J-head-hotend-RepRap-Rostock-Bowden/1962255_32837262661.html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)
2 | M3 Wing Nuts (pack of 10) | $1.93 | Aliexpress | | . (https://www.aliexpress.com/item/10Pcs-M3-M4-M5-M6-M8-DIN315-304-Stainless-Steel-Hand-Tighten-Nut-Butterfly-Nut-Ingot/32867916920.html)
1 | Power Cord 10A NEMA 5-15P to C13 | $7.50 | Amazon | | . (https://www.amazon.com/SF-Cable-Universal-Power-IEC320/dp/B006W0IIZ6)

https://www.aliexpress.com/store/product/2pcs-8mm-8x400-linear-shaft-3d-printer-8mm-x-400mm-Cylinder-Liner-Rail-Linear-Shaft-axis/1762258_32332798910.html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
https://www.aliexpress.com/store/product/2pcs-8mm-8x400-linear-shaft-3d-printer-8mm-x-400mm-Cylinder-Liner-Rail-Linear-Shaft-axis/1762258_32332798910.html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,searchweb201602_4_10152_10065_10151_10344_10068_10130_10342_10547_10343_10546_10340_5724715_10548_10341_10545_10696_10084_5724015_10083_10618_5724315_10307_5724215_5724115_10059_100031_5725015_10103_5724915_10624_10623_10622_10621_10620,searchweb201603_45,ppcSwitch_7&algo_expid=6f89a215-e6c6-4883-a54c-334774792524-2&algo_pvid=6f89a215-e6c6-4883-a54c-334774792524&priceBeautifyAB=0 https://www.aliexpress.com/store/product/4pcs-lot-Free-shipping-LM12UU-Linear-Bushing-12mm-CNC-Linear-Bearings/1762258_32317273540.html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,searchweb201602_4_10152_10065_10151_10344_10068_10130_10342_10547_10343_10546_10340_5724715_10548_10341_10545_10696_10084_5724015_10083_10618_5724315_10307_5724215_5724115_10059_100031_5725015_10103_5724915_10624_10623_10622_10621_10620,searchweb201603_45,ppcSwitch_7&algo_expid=6f89a215-e6c6-4883-a54c-334774792524-2&algo_pvid=6f89a215-e6c6-4883-a54c-334774792524&priceBeautifyAB=0 https://www.aliexpress.com/store/product/2pcs-TR8x8-TR8x4-TR8x2-8mm-Acme-Anti-Backlash-Nut-Block-for-CNC-3D-printer-spare-parts/2412069_32809617055.html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,searchweb201602_4_10152_10151_10065_10344_10068_10130_10324_10342_10547_10325_10343_10546_10340_10548_10341_315_10545_10696_10084_531_10083_10618_10307_5013515_5013615_10059_100031_5013415_10103_5013315_10624_10623_10622_10621_10620,searchweb201603_45,ppcSwitch_7&algo_expid=3f7546ee-a53d-4a87-acc4-f97c58db8ee8-0&algo_pvid=3f7546ee-a53d-4a87-acc4-f97c58db8ee8&priceBeautifyAB=0 https://www.aliexpress.com/item/Nema17-17HS4401-stepper-motor-with-T8-screw-lead-8mm-300-400-500mm-42-motor-42BYGH-3D/32888650990.html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
https://www.aliexpress.com/store/product/Free-shipping-3PCS-4-lead-Nema17-Stepper-Motor-42-motor-17HS8401S-1-8A-CE-ROSH-ISO/432672_32819461559.html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,searchweb201602_4_10152_10065_10151_10344_10068_10130_10342_10547_10343_10546_10340_10341_10548_5724715_315_10545_10696_10084_531_5724015_10083_10618_5724315_10307_5724215_5724115_10059_100031_5725015_10103_5724915_10624_10623_10622_10621_10620-normal#cfs,searchweb201603_55,ppcSwitch_7&algo_expid=29685acb-edd2-4aaf-84df-2d0d8503f228-6&algo_pvid=29685acb-edd2-4aaf-84df-2d0d8503f228&priceBeautifyAB=0 https://www.aliexpress.com/store/product/4PCS-EDL-30mm-15Kg-PA-Nylon-furniture-Castors-Wheels-Plate-Brake-Locking-Small-Furniture-Caster-Wheels/1994013_32830437491.h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,searchweb201602_4_10152_10065_10151_10344_10068_10130_10342_10547_10343_10546_10340_10341_10548_5724715_315_10545_10696_10084_531_5724015_10083_10618_5724315_10307_5724215_5724115_10059_100031_5725015_10103_5724915_10624_10623_10622_10621_10620,searchweb201603_55,ppcSwitch_7&algo_expid=f04f4038-05af-4ee1-85eb-3de7d4ee4994-15&algo_pvid=f04f4038-05af-4ee1-85eb-3de7d4ee4994&priceBeautifyAB=0 https://www.aliexpress.com/store/product/10pcs-GT2-Idler-Timing-Pulley-16-20-Tooth-Wheel-Bore-3-5mm-Aluminium-Gear-Teeth-Width/432672_32822906447.html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
https://www.aliexpress.com/store/product/3D-Printer-Parts-Accessory-GT2-16teeth-16-teeth-Bore-5mm-Timing-Alumium-Pulley-fit-for-GT2/432672_32784183624.html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,searchweb201602_4_10152_10065_10151_10344_10068_10130_10342_10547_10343_10546_10340_10341_10548_5724715_315_10545_10696_10084_531_5724015_10083_10618_5724315_10307_5724215_5724115_10059_100031_5725015_10103_5724915_10624_10623_10622_10621_10620,searchweb201603_55,ppcSwitch_7&algo_expid=a6d89d6a-752b-4b34-8a84-a43696daed41-34&algo_pvid=a6d89d6a-752b-4b34-8a84-a43696daed41&priceBeautifyAB=0 https://www.aliexpress.com/store/product/5m-lot-GT2-6mm-open-timing-belt-width-6mm-GT2-belt-Rubbr-Fiberglass-cut-to-length/2498059_32811832945.html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,searchweb201602_4_10065_10068_5910015_10130_10547_10546_5890015_10548_5724715_315_10545_10696_531_10084_5724015_10083_5970015_10618_5724315_10307_5724215_5724115_10059_5860016_100031_5725015_10103_5725115_5980015_5724915_5990015,searchweb201603_56,ppcSwitch_7&algo_expid=404ee00f-aaa4-41b3-aa72-99e7f90db33f-3&algo_pvid=404ee00f-aaa4-41b3-aa72-99e7f90db33f&priceBeautifyAB=0 https://www.aliexpress.com/item/1PCS-YT784-Thickening-Stainless-Steel-Bracket-Rectangular-L-Fixed-Bracket-Furniture-Fastening-accessories-20-20-16mm/32775929759.html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 https://www.aliexpress.com/store/product/100pcs-50pcs-3030-Aluminum-Profile-with-Slot-Groove-8mm-M4-M5-M6-Nickel-Plated-T-Bolt/937165_32825325332.html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,searchweb201602_4_10065_10068_5910015_10130_10547_5890015_10546_10548_5724715_315_10545_10696_10084_531_5724015_10083_5970015_10618_5724315_10307_5724215_5724115_10059_100031_5725015_10103_5980015_5724915_5990015,searchweb201603_56,ppcSwitch_7&algo_expid=f7ac111b-a1cf-462f-89d5-95237e8d5609-0&algo_pvid=f7ac111b-a1cf-462f-89d5-95237e8d5609&priceBeautifyAB=0 https://us.misumi-ec.com/vona2/detail/110302686450/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 https://us.misumi-ec.com/vona2/detail/110302686450/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 https://us.misumi-ec.com/vona2/detail/110302686450/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 https://www.mcmaster.com/4568t12
https://www.ikea.com/us/en/catalog/products/60193736/
https://www.gamut.com/p/pan-head-machine-screw-steel-zinc-plated-phillips-m3-thread-size-NDAyNTU
https://www.gamut.com/p/hex-nut-steel-plain-class-8-material-grade-m3-thread-size-ODU4MQ
https://www.gamut.com/p/pan-head-machine-screw-steel-zinc-plated-phillips-m6-thread-size-NTQxMQhttps://www.aliexpress.com/store/product/Hex-Head-Socket-Cap-Set-Grub-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 https://www.aliexpress.com/store/product/Link-End-Parallel-Side-by-Side-Vertical-Joint-Connect-Angle-Connector-Strip-for-2020-20x20-Aluminum/937165_2043798062.html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
https://www.aliexpress.com/store/product/DuoWeiSi-3D-Printer-Parts-300x300mm-120V-750W-Silicone-Heater-Pad-For-3D-Printer-Heated-Bed-Heating/2882163_32822542158.html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,searchweb201602_4_10065_10068_10130_10890_5730315_10547_319_10546_10548_317_10545_10696_10924_453_10084_454_10083_10618_10920_5729215_10921_10922_10307_537_536_10059_10884_10887_10928_100031_321_322_10103,searchweb201603_51,ppcSwitch_0&algo_expid=a58e76dd-633b-4b3b-bc00-aae51c7ed1f1-0&algo_pvid=a58e76dd-633b-4b3b-bc00-aae51c7ed1f1 https://www.aliexpress.com/item/M3-M4-M5-M6-M8-M20-Large-Flat-Washer-304-Stainless-Steel-Big-Metal-Gasket-Meson/32847105986.html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,searchweb201602_4_10065_10068_10130_10890_5730315_10547_319_10546_10548_317_10545_10696_10924_453_10084_454_10083_10618_10920_5729215_10921_10922_10307_537_536_10059_10884_10887_10928_100031_321_322_10103-5729215,searchweb201603_51,ppcSwitch_0&algo_expid=9582f57f-5fac-4c1c-926f-e11e940ae0d9-3&algo_pvid=9582f57f-5fac-4c1c-926f-e11e940ae0d9 https://www.aliexpress.com/item/1pcs-Free-shipping-solid-state-relay-SSR-10DA-10A-actually-3-32V-DC-TO-24-380V/32706812752.html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,searchweb201602_4_10065_10068_10130_10890_5730315_10547_319_10546_10548_317_10545_10696_10924_453_10084_454_10083_10618_10920_5729215_10921_10922_10307_537_536_10059_10884_10887_10928_100031_321_322_10103,searchweb201603_51,ppcSwitch_0&algo_expid=0f19c8e6-3dbc-47c7-aeb0-e5c3f13d3a5d-2&algo_pvid=0f19c8e6-3dbc-47c7-aeb0-e5c3f13d3a5d https://www.aliexpress.com/item/10Pcs-lot-100K-ohm-NTC-3950-Thermistors-for-3D-Printer-Reprap-Mend-Free-Shipping/32639944762.html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,searchweb201602_4_10065_10068_10130_10890_5730315_10547_319_10546_10548_317_10545_10696_10924_453_10084_454_10083_10618_10920_5729215_10921_10922_10307_537_536_10059_10884_10887_10928_100031_321_322_10103,searchweb201603_51,ppcSwitch_0&algo_expid=106660f0-84e5-4275-b93e-ef2059bc4bd6-1&algo_pvid=106660f0-84e5-4275-b93e-ef2059bc4bd6 https://www.midweststeelsupply.com/store/castaluminumplateatp5
https://www.gamut.com/p/pan-head-machine-screw-steel-zinc-plated-phillips-m6-thread-size-MTA4NTk1
https://www.gamut.com/p/nylon-spacer-metric-black-m3-screw-size-10-mm-overall-lg-MzYyMTY
https://www.gamut.com/p/pan-head-machine-screw-steel-zinc-plated-phillips-m3-thread-size-ODk1MDI
https://www.gamut.com/p/pan-head-machine-screw-steel-zinc-plated-phillips-m3-thread-size-MTEyOTUhttps://www.aliexpress.com/item/Blue-White-PVC-Pipe-OD-20mm-25mm-32mm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,searchweb201602_4_10065_10068_10130_10890_5730315_10547_319_10546_317_10548_10545_5728815_10696_10084_10083_10618_5729215_10307_5733215_5733315_328_10059_10884_10887_5733115_100031_5733415_321_322_5732515_10103_5733515_5733615,searchweb201603_55,ppcSwitch_0&algo_expid=8554709a-4fd6-4201-8d89-35ada7212b0e-10&algo_pvid=8554709a-4fd6-4201-8d89-35ada7212b0e https://www.aliexpress.com/item/Hot-Sale-AC85-265V-110V-220V-to-DC5V-12V-24V-36V-48V-1A-2A-3A-5A/32780272089.html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,searchweb201602_4_10065_10068_10130_5731315_10890_5730315_10547_319_10546_10548_317_10545_5728815_10696_10084_10083_10618_5729215_10307_5731115_5731415_5731215_5731615_5732015_328_10059_10884_5731515_10887_100031_321_322_5732515_10103_5731715-10890_5731415,searchweb201603_55,ppcSwitch_0&algo_expid=1bf5639b-90aa-4ffe-8363-7185726115fd-1&algo_pvid=1bf5639b-90aa-4ffe-8363-7185726115fd https://www.aliexpress.com/item/Baomain-IEC-320-C14-Red-Light-Rocker-Inlet-Male-Power-Supply-Connector-Plug/32706948395.html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,searchweb201602_4_10065_10068_10130_10890_10547_10546_319_10548_317_5733420_10545_10696_10924_453_10084_10925_454_10083_10926_5733620_10618_10920_10921_10922_10307_5733120_5733220_537_536_5733320_5733520_10059_10884_5730320_10887_10928_100031_321_322_10103_5729220-5733320,searchweb201603_51,ppcSwitch_0&algo_expid=32d6aa12-b1b5-4f57-8b69-f5c5fc86142e-3&algo_pvid=32d6aa12-b1b5-4f57-8b69-f5c5fc86142e https://www.aliexpress.com/item/Silica-Gel-Box-1pc-Reusable-White-Orange-Blue-Silicagel-Moisture-Absorber-Absorbent-Desiccant-Box-Color-Changing/32793744530.html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,searchweb201602_4_10065_10068_10130_10890_5730315_10547_319_10546_317_10548_10545_5728815_10696_10084_10083_10618_5729215_10307_5733215_5733315_328_10059_10884_10887_5733115_100031_5733415_321_322_5732515_10103_5733515_5733615,searchweb201603_55,ppcSwitch_0&algo_expid=ce2a4ff8-5c53-450f-bbf6-271fd255368b-0&algo_pvid=ce2a4ff8-5c53-450f-bbf6-271fd255368b https://www.aliexpress.com/store/product/CNC-3D-Printer-Kit-for-Arduino-Mega-2560-R3-RAMPS-1-4-Controller-LCD-12864-6/415445_32685004463.html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,searchweb201602_4_10065_10068_5910015_10130_5723115_10547_5723715_10546_5890015_10548_5724715_5723815_315_10545_10696_5723215_5724015_5723415_531_10084_10083_5970015_10618_5724315_10307_5724215_5724115_5723315_5723615_10059_5723015_5860016_100031_5723915_5725015_10103_5725115_5980015_5724915_5990015-5990015,searchweb201603_54,ppcSwitch_7&algo_expid=d8550be4-5b09-4ef8-b376-777a7e339b51-0&algo_pvid=d8550be4-5b09-4ef8-b376-777a7e339b51&priceBeautifyAB=0 https://www.aliexpress.com/item/50Meter-6-7-8-10-11-12-13-14-15-16-17-18-20-22-24/32718990317.html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,searchweb201602_4_10065_10068_10130_10890_10547_319_10546_10548_317_10545_5730313_10696_10924_453_10084_10925_454_10083_10926_10618_5729213_10920_10921_10922_10307_537_536_5733211_5733311_10059_10884_5733113_10887_10928_100031_321_5733413_322_10103_5733613_5733511-5729213_5733211,searchweb201603_51,ppcSwitch_0&algo_expid=9b1ba8d1-3e25-4aed-8d8c-7757a30e899b-2&algo_pvid=9b1ba8d1-3e25-4aed-8d8c-7757a30e899b https://www.aliexpress.com/item/1pcs-Clear-Acrylic-Perspex-Sheet-Cut-Plastic-Transparent-Board-Perspex-Panel-2-5mm-thickness/32850622506.html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,searchweb201602_4_5852211_10065_10068_10130_5852513_5730315_10890_10547_319_10546_5853215_317_10548_10545_5851613_10696_5852411_5853015_10924_10084_453_10925_10083_454_10926_10618_10920_10921_5729215_10922_5852915_10307_5850015_537_536_5733215_5733315_5850913_10059_10884_10887_5733115_10928_100031_5733415_321_322_10103_5733613_5852713_5852612_5733515-10890,searchweb201603_51,ppcSwitch_0&algo_expid=31742d67-e56e-4212-a2ab-610d05458624-1&algo_pvid=31742d67-e56e-4212-a2ab-610d05458624 https://www.aliexpress.com/item/10Pcs-Durable-Clear-Acrylic-Plastic-Folding-Hinges-Plexiglass-Hinge/32889707845.html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,searchweb201602_4_10065_10130_10068_10547_10890_5730315_10546_5853215_10548_5851615_10545_10696_5853015_10924_10925_10926_10618_10920_5729215_10921_10307_5852915_10922_537_536_10059_100031_10103_319_317_5852213_5852515_5852413_453_10084_454_10083_5850015_5733215_5733315_10884_5850915_5733115_10887_10928_5733415_321_322_5852715_5733515_5852615_5733615-10890,searchweb201603_51,ppcSwitch_0&algo_expid=2622abaa-9fc4-48b9-9a1d-9e93bfd7ac21-2&algo_pvid=2622abaa-9fc4-48b9-9a1d-9e93bfd7ac21 https://www.aliexpress.com/item/3D-Printer-Parts-DIY-Titan-Extruder-Fully-Kits-With-Nema-17-Stepper-Motor-For-V6-J/32865543307.html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,searchweb201602_4_10065_10068_10130_10890_5730315_10547_319_10546_317_10548_10545_5728815_10696_10084_10083_10618_5729215_10307_5733215_5733315_328_10059_10884_10887_5733115_100031_5733415_321_322_5732515_10103_5733515_5733615,searchweb201603_55,ppcSwitch_0&algo_expid=4a3f6935-3922-470a-81fe-bd1eeab80136-14&algo_pvid=4a3f6935-3922-470a-81fe-bd1eeab80136 https://www.aliexpress.com/store/product/Hot-1M-PTFE-Tube-Teflon-PC4-M6-PC4-01-Fitting-J-head-hotend-RepRap-Rostock-Bowden/1962255_32837262661.html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,searchweb201602_4_10152_10151_10065_10344_10068_10130_10324_10342_10547_10325_10343_10546_10340_10548_10341_315_10545_10696_5013115_10084_531_10083_10618_10307_10059_100031_5013415_5013215_10103_5013315_10624_10623_10622_10621_10620,searchweb201603_45,ppcSwitch_7&algo_expid=4cc219ef-4a38-4dc5-878e-afabc5ff41ab-37&algo_pvid=4cc219ef-4a38-4dc5-878e-afabc5ff41ab&priceBeautifyAB=0 https://www.aliexpress.com/item/10Pcs-M3-M4-M5-M6-M8-DIN315-304-Stainless-Steel-Hand-Tighten-Nut-Butterfly-Nut-Ingot/32867916920.html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,searchweb201602_4_10065_10130_10068_10547_10890_5730315_10546_5853215_10548_10545_10696_5851613_5853015_10924_10925_10926_10618_10920_5729215_10921_10307_5852915_10922_537_536_10059_100031_10103_5852211_319_317_5852515_5852412_453_10084_454_10083_5850015_5733215_5733315_5850913_10884_5733115_10887_10928_5733415_321_322_5852713_5852613_5733515_5733615-5733215,searchweb201603_51,ppcSwitch_0&algo_expid=0c2a1c57-90f4-4816-a290-da1cbaa90198-0&algo_pvid=0c2a1c57-90f4-4816-a290-da1cbaa90198 https://www.amazon.com/SF-Cable-Universal-Power-IEC320/dp/B006W0IIZ6/ref=cm_cr_arp_d_product_top?ie=UTF8

Parts and Materials Purchased
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

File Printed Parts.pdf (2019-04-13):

Printed Parts

# Printed Parts

Part Name | Version Number | Amount to print | Notes
| | Parts for IKEA Lack Tables
Acrylic Panel Clamp | 2.4 | 16 | Used to clamp down side panels (on left and right of top IKEA Lack table)
Acrylic Toggle Clamp Base | 3.1 | 10 | Part of the toggle clamp used to clamp front and back acrylic panels
Acrylic Toggle Clamp Connector | 2 | 20 | Part of the toggle clamp used to clamp front and back acrylic panels
Acrylic Toggle Clamp Lever | 3 | 10 | Part of the toggle clamp used to clamp front and back acrylic panels
Acrylic Toggle Clamp Handle | 4.2 | 10 | Part of the toggle clamp used to clamp front and back acrylic panels
Acrylic Toggle Clamp Moving Clamp | 1.1 | 10 | Part of the toggle clamp used to clamp front and back acrylic panels
Caster Adapter for IKEA Lack | 1 | 4 | Caster connector to IKEA Lack table leg
LCD and Controls Case | 3.1 | 1 | Needs modification: side needs to be clipped of for access of SD card slot
PVC Pipe Clamp | 2 | 4
PVC Pipes Joiner | 1.1 | 4
Reinforcement and Mounting Bracket for IKEA Lack Type 1 | 2 | 4 | Goes on underside of bottom table
Reinforcement and Mounting Bracket for IKEA Lack Type 2 | 2 | 8 | Goes on top of bottom table and underside of top table
Switch Holder | 1 | 1 | Placed on left (or right) leg on the front side (side with LCD screen) of the bottom IKEA Lack table
Wire Clamp | 1 | As needed (around 11)
Hotend Carriage
Bronze Bushing Holder from Bushing Holder V5.1 | 5.1 | 3 | Bushing holder/spacer for X axis hotend carriage
Carriage Main for X axis | 3 | 1
Fan Air Vent/Director | 2 | 1 | Addition of tape potentially needed to make the friction fit that is required
GT2 Belt Clamp | 1 | 2
Hotend Clamp Top for V3 of Hotend Carriage | 3 | 1
Hotend Mount Plate for V3 of Hotend Carriage | 3 | 1 | Install hotend and this clamp before attaching fan
X and Y axes
12mm Steel Rod Clamp Type 1 | 2.3 | 2
12mm Steel Rod Clamp Type 2 | 2.4 | 2
Endstop Mount 9.525mm (X axis clamp rotated) | 6 | 1
Endstop Mount 12mm | 3.5 | 1
Idler Bearing Mount | 1.3 | 2
Motor Mount | 1.5 | 2
XY Joiner | 1.5 | 2
Z axis
Endstop Mount 10mm (opposite orientation of endstop) | 5.1 | 1 | M3 holes need drilling through. Endstop installs with PCB side facing out
Z axis Adjustable Screw | 1.1 | 1
Z Bearing to Bed | 3.1 | 2
Z Lead Screw Restraint | 1 | 1
Z Lead Screw Nut to Bed Mount | 1.1 | 1
Z Motor Mount | 1 | 1
Z axis 10mm Rod Clamp Front-Left | 1.2 | 2
Z axis 10mm Rod Clamp Front-Right | 1.2 | 2
Other
Extruder Mount | 1 | 1
Filament Runout Sensor Clip | 4 | 1
Hotend Wire Clamp Part 1 | 2 | 1
Hotend Wire Clamp Part 2 | 2 | 1
M6x8.5 Spacer, wider | 1 | As needed

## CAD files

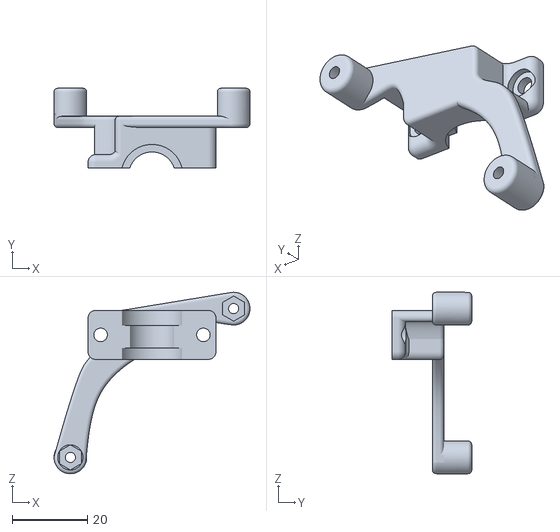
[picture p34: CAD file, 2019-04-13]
STL files/Hotend Carriage/X axis Hotend Carriage V3 Hotend Plate Top .stl
52.1 x 21.1 x 48.3

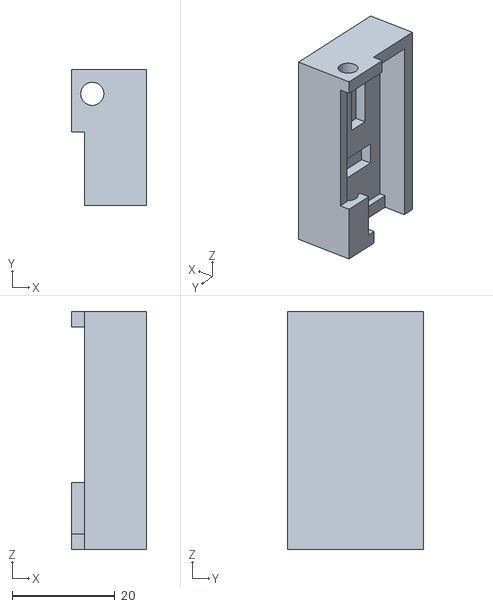
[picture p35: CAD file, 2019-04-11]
STL files/Other/Filament Runout Sensor Clip V4.stl
14.5 x 26.5 x 46.3

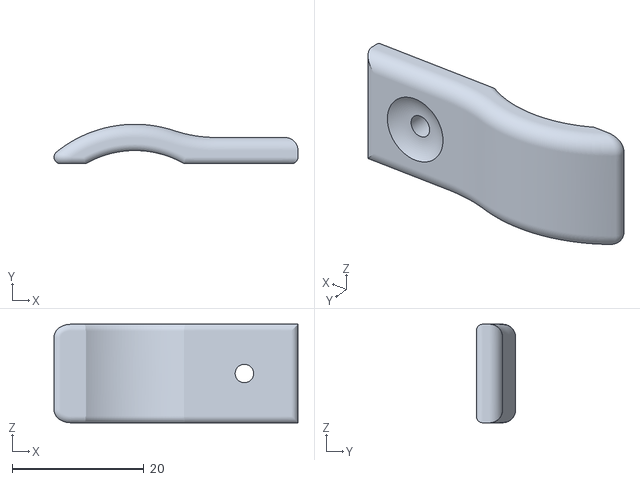
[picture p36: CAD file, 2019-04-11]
STL files/Parts for IKEA Lack tables/Wire Clamp V1.stl
37.1 x 6.00 x 15.0

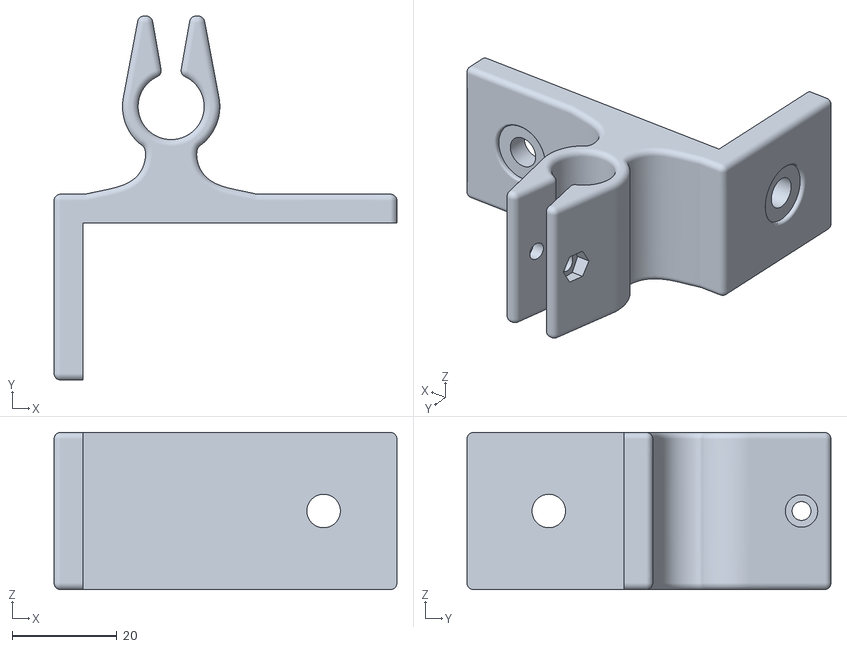
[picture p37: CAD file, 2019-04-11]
STL files/XY axes/12mm Steel Rod Clamp V2.3.stl
65.5 x 69.5 x 30.0

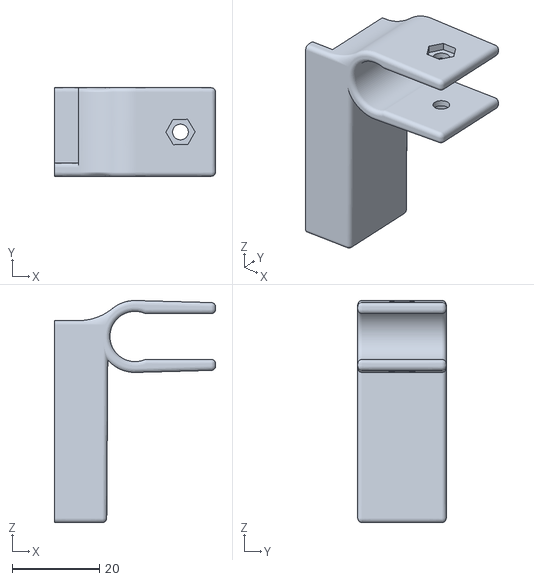
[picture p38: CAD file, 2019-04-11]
STL files/Z axis/Endstop Mount 10mm Z axis V5.1 opp. orient..stl
37.0 x 20.3 x 50.9

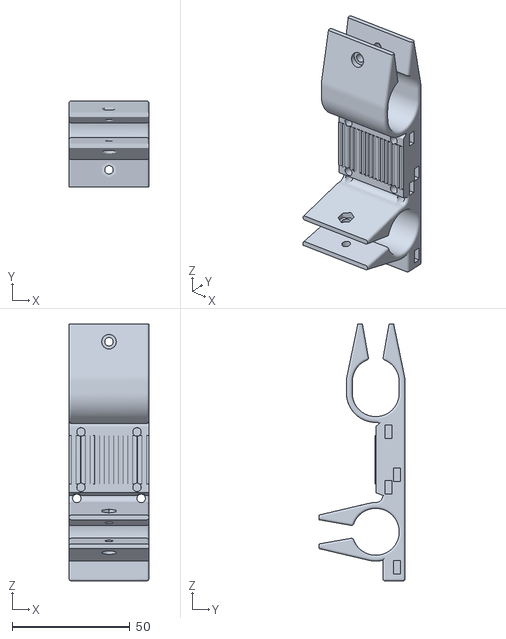
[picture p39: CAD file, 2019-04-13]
STL files/Hotend Carriage/X axis Hotend Carriage V3.stl
34.0 x 36.6 x 109.2

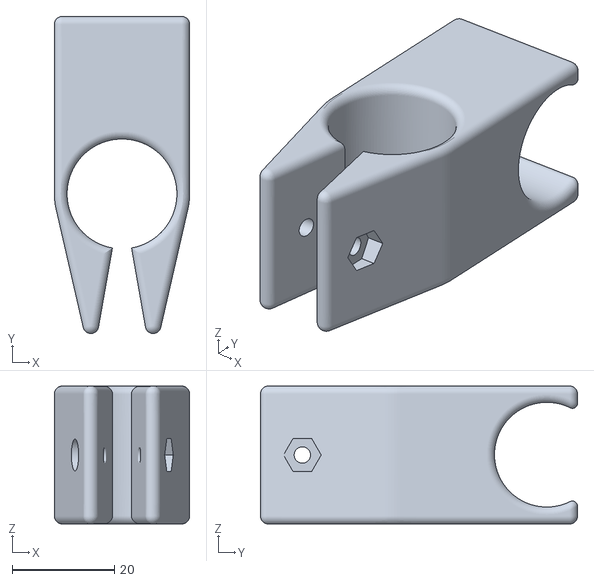
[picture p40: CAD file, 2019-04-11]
STL files/Parts for IKEA Lack tables/PVC Pipes Joiner V1.1.stl
26.5 x 62.1 x 27.0

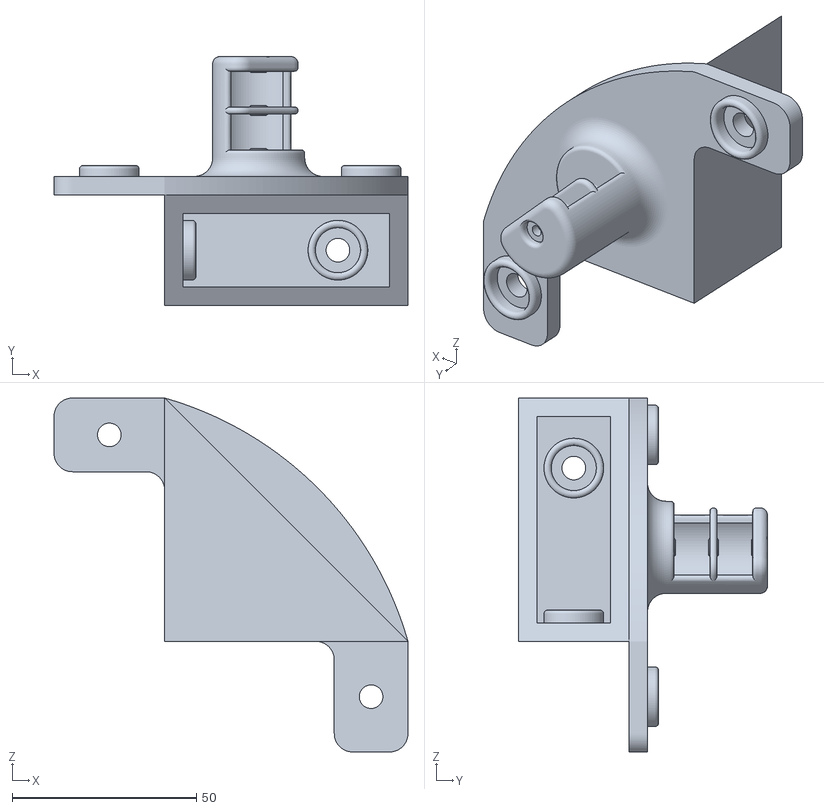
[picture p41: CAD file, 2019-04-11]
STL files/XY axes/Idler Bearing Mount V1.3.stl
96.0 x 67.5 x 96.0

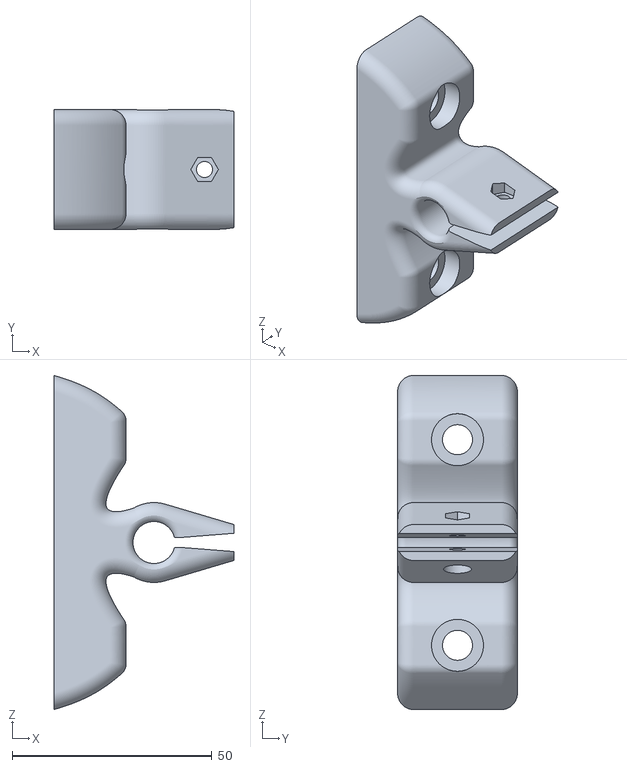
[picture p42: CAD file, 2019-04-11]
STL files/Z axis/Z-axis 10mm Rod Clamp, Front-Right, V1.2.stl
45.0 x 30.0 x 83.6

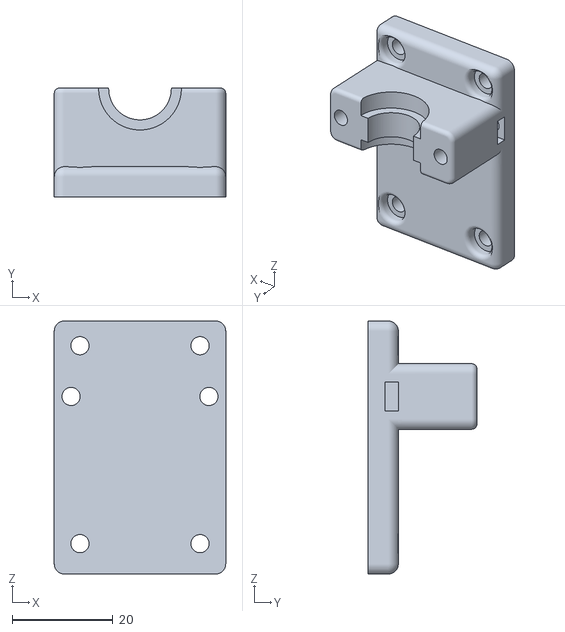
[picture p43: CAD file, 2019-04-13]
STL files/Hotend Carriage/X axis Hotend Carriage V3 Hotend Plate.stl
34.0 x 21.6 x 50.1

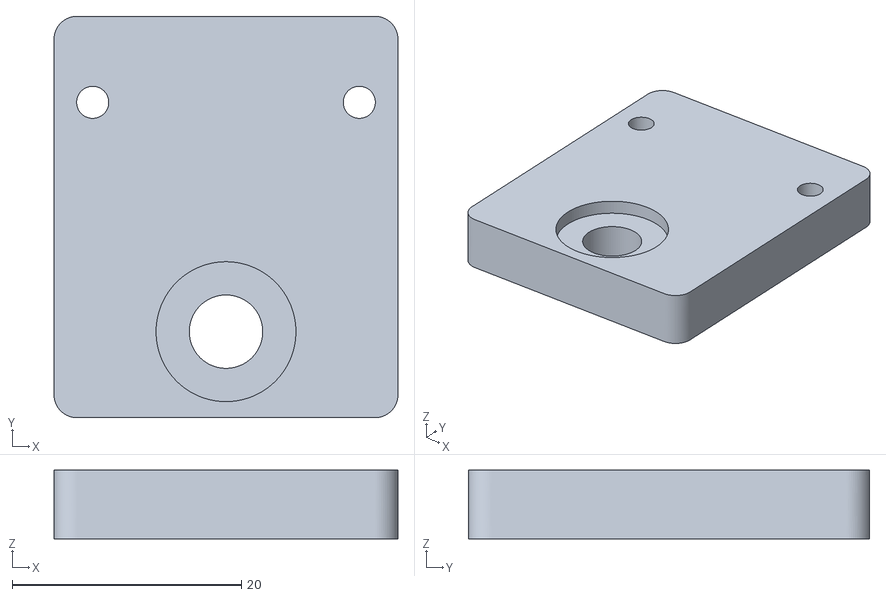
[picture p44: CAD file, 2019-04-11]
STL files/Other/Hotend Wire Clamp Part 2 V2.stl
30.0 x 35.0 x 6.00

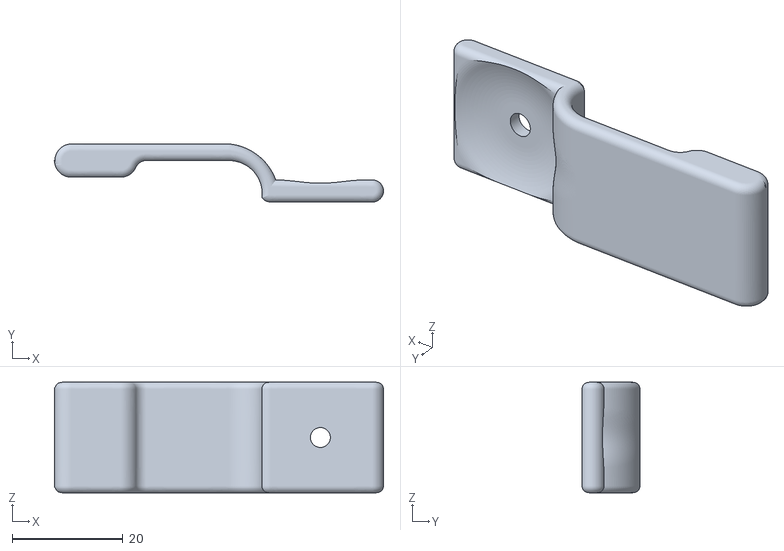
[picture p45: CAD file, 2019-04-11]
STL files/Parts for IKEA Lack tables/Acrylic Panel Clamp V2.4.stl
59.5 x 10.5 x 20.0

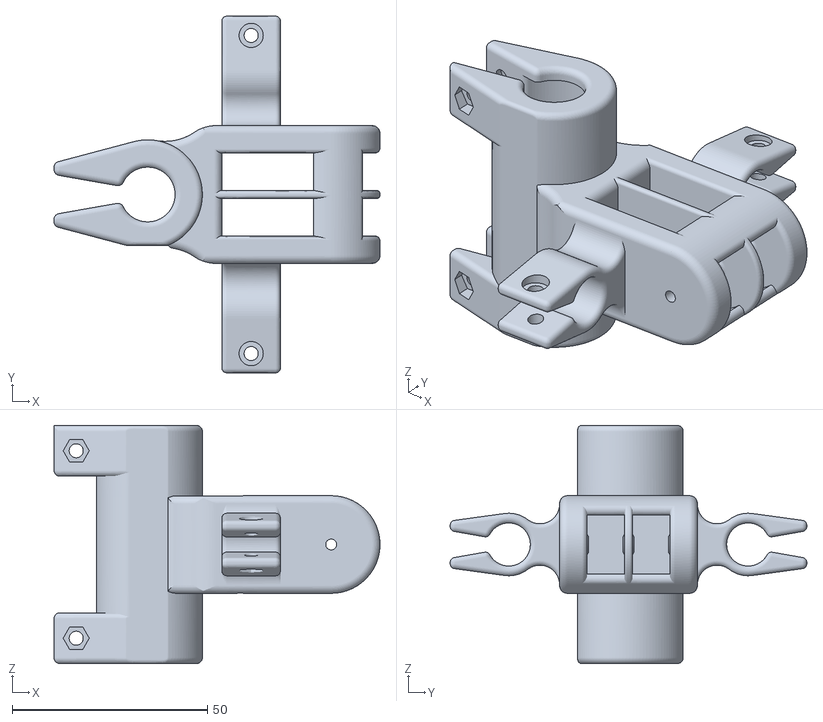
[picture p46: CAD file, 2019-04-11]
STL files/XY axes/XY Joiner V1.5.stl
83.5 x 91.3 x 61.0

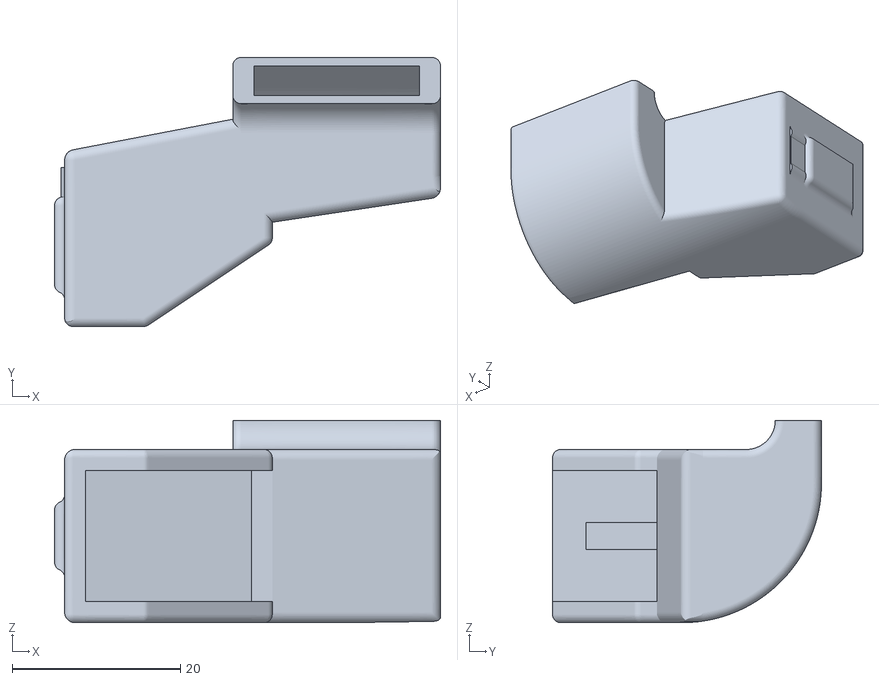
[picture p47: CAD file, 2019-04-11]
STL files/Hotend Carriage/Fan Air Vent V2.stl
45.9 x 32.0 x 24.1

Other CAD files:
STL files/Other/Hotend Wire Clamp Part 1 V2.stl
STL files/XY axes/Endstop Mount 12mm Rod V3.5.stl
STL files/Z axis/Z-axis 10mm Rod Clamp, Front-Left, V1.2.stl
STL files/Hotend Carriage/Bronze Bushing Holder from Bushing Holder V5.1.stl
STL files/Hotend Carriage/GT2 Belt Clamp V1.stl
STL files/Other/Extruder Mount V1.stl
STL files/Other/M6x8.5 Spacer, wider.stl
STL files/Parts for IKEA Lack tables/Acrylic Toggle Clamp V1.1 5-Moving Clamp.stl
STL files/Parts for IKEA Lack tables/Acrylic Toggle Clamp V2 2-Connector.stl
STL files/Parts for IKEA Lack tables/Acrylic Toggle Clamp V3 3-Lever.stl
STL files/Parts for IKEA Lack tables/Acrylic Toggle Clamp V3 4-Handle.stl
STL files/Parts for IKEA Lack tables/Acrylic Toggle Clamp V3.1 1-Base.stl
STL files/Parts for IKEA Lack tables/Acrylic Toggle Clamp V4.2 4-Handle.stl
STL files/Parts for IKEA Lack tables/Caster Adapterfor IKEA Lack.stl
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

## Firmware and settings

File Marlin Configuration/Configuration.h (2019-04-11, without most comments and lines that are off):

#define CONFIGURATION_H
#define CONFIGURATION_H_VERSION 010109
#define STRING_CONFIG_H_AUTHOR "(none, default config)" // Who made the changes.
#define SHOW_BOOTSCREEN
#define STRING_SPLASH_LINE1 SHORT_BUILD_VERSION // will be shown during bootup in line 1
#define STRING_SPLASH_LINE2 WEBSITE_URL         // will be shown during bootup in line 2
#define SERIAL_PORT 0
#define BAUDRATE 250000
  #define MOTHERBOARD 43 //orig. BOARD_RAMPS_14_EFB CHANGED
#define EXTRUDERS 1
#define DEFAULT_NOMINAL_FILAMENT_DIA 1.75 //3.0
#define POWER_SUPPLY 0
#define TEMP_SENSOR_0 1 //CHANGED
#define TEMP_SENSOR_1 0
#define TEMP_SENSOR_2 0
#define TEMP_SENSOR_3 0
#define TEMP_SENSOR_4 0
#define TEMP_SENSOR_BED 1 //CHANGED from 0
#define TEMP_SENSOR_CHAMBER 0
#define DUMMY_THERMISTOR_998_VALUE 25
#define DUMMY_THERMISTOR_999_VALUE 100
#define MAX_REDUNDANT_TEMP_SENSOR_DIFF 10
#define TEMP_RESIDENCY_TIME 10  // (seconds)
#define TEMP_HYSTERESIS 3       // (degC) range of +/- temperatures considered "close" to the target one
#define TEMP_WINDOW     1       // (degC) Window around target to start the residency timer x degC early.
#define TEMP_BED_RESIDENCY_TIME 10  // (seconds)
#define TEMP_BED_HYSTERESIS 3       // (degC) range of +/- temperatures considered "close" to the target one
#define TEMP_BED_WINDOW     1       // (degC) Window around target to start the residency timer x degC early.
#define HEATER_0_MINTEMP 5
#define HEATER_1_MINTEMP 5
#define HEATER_2_MINTEMP 5
#define HEATER_3_MINTEMP 5
#define HEATER_4_MINTEMP 5
#define BED_MINTEMP 5
#define HEATER_0_MAXTEMP 275
#define HEATER_1_MAXTEMP 275
#define HEATER_2_MAXTEMP 275
#define HEATER_3_MAXTEMP 275
#define HEATER_4_MAXTEMP 275
#define BED_MAXTEMP 150
#define PIDTEMP
#define BANG_MAX 255     // Limits current to nozzle while in bang-bang mode; 255=full current
#define PID_MAX BANG_MAX // Limits current to nozzle while PID is active (see PID_FUNCTIONAL_RANGE below); 255=full current
#define PID_K1 0.95      // Smoothing factor within any PID loop
  #define PID_FUNCTIONAL_RANGE 10 // If the temperature difference between the target temperature and the actual temperature
  #define DEFAULT_Kp 27.71 //CHANGED
  #define DEFAULT_Ki 2.97 //CHANGED
  #define DEFAULT_Kd 64.69 //CHANGED
#define PIDTEMPBED //CHANGED from comment
#define MAX_BED_POWER 255 // limits duty cycle to bed; 255=full current
  #define DEFAULT_bedKp 38.98 //CHANGED
  #define DEFAULT_bedKi 0.71 //CHANGED
  #define DEFAULT_bedKd 534.88 //CHANGED
#define PREVENT_COLD_EXTRUSION
#define EXTRUDE_MINTEMP 170
#define PREVENT_LENGTHY_EXTRUDE
#define EXTRUDE_MAXLENGTH 200
#define THERMAL_PROTECTION_HOTENDS // Enable thermal protection for all extruders
#define THERMAL_PROTECTION_BED     // Enable thermal protection for the heated bed
#define COREXY // CHANGED
#define USE_XMIN_PLUG
#define USE_YMIN_PLUG
#define USE_ZMIN_PLUG
#define ENDSTOPPULLUPS
#define X_MIN_ENDSTOP_INVERTING true // set to true to invert the logic of the endstop. //CHANGED all to true
#define Y_MIN_ENDSTOP_INVERTING true // set to true to invert the logic of the endstop.
#define Z_MIN_ENDSTOP_INVERTING true // set to true to invert the logic of the endstop.
#define X_MAX_ENDSTOP_INVERTING true // set to true to invert the logic of the endstop.
#define Y_MAX_ENDSTOP_INVERTING true // set to true to invert the logic of the endstop.
#define Z_MAX_ENDSTOP_INVERTING true // set to true to invert the logic of the endstop.
#define Z_MIN_PROBE_ENDSTOP_INVERTING false // set to true to invert the logic of the probe.
#define X_DRIVER_TYPE  A4988  //CHANGED uncommented
#define Y_DRIVER_TYPE  A4988  //CHANGED uncommented
#define Z_DRIVER_TYPE  A4988  //CHANGED uncommented
#define E0_DRIVER_TYPE A4988 //CHANGED uncommented
#define DEFAULT_AXIS_STEPS_PER_UNIT   { 100, 100, 400, 500 } //CHANGED
#define DEFAULT_MAX_FEEDRATE          { 300, 300, 5, 25 }
#define DEFAULT_MAX_ACCELERATION      { 3000, 3000, 100, 10000 } //CHANGED was 3000,3000,100,10000
#define DEFAULT_ACCELERATION          2000    // X, Y, Z and E acceleration for printing moves CHANGED from 3000
#define DEFAULT_RETRACT_ACCELERATION  3000    // E acceleration for retracts
#define DEFAULT_TRAVEL_ACCELERATION   2000    // X, Y, Z acceleration for travel (non printing) moves CHANGED from 3000
#define DEFAULT_XJERK                 5.0 //CHANGED
#define DEFAULT_YJERK                 5.0 //CHANGED
#define DEFAULT_ZJERK                  0.3
#define DEFAULT_EJERK                  5.0
#define S_CURVE_ACCELERATION //CHANGED uncommented
#define Z_MIN_PROBE_USES_Z_MIN_ENDSTOP_PIN
#define X_PROBE_OFFSET_FROM_EXTRUDER 10  // X offset: -left  +right  [of the nozzle]
#define Y_PROBE_OFFSET_FROM_EXTRUDER 10  // Y offset: -front +behind [the nozzle]
#define Z_PROBE_OFFSET_FROM_EXTRUDER 0   // Z offset: -below +above  [the nozzle]
#define MIN_PROBE_EDGE 10
#define XY_PROBE_SPEED 8000
#define Z_PROBE_SPEED_FAST HOMING_FEEDRATE_Z
#define Z_PROBE_SPEED_SLOW (Z_PROBE_SPEED_FAST / 2)
#define Z_CLEARANCE_DEPLOY_PROBE   10 // Z Clearance for Deploy/Stow
#define Z_CLEARANCE_BETWEEN_PROBES  5 // Z Clearance between probe points
#define Z_CLEARANCE_MULTI_PROBE     5 // Z Clearance between multiple probes
#define Z_PROBE_LOW_POINT          -2 // Farthest distance below the trigger-point to go before stopping
#define Z_PROBE_OFFSET_RANGE_MIN -20
#define Z_PROBE_OFFSET_RANGE_MAX 20
#define X_ENABLE_ON 0
#define Y_ENABLE_ON 0
#define Z_ENABLE_ON 0
#define E_ENABLE_ON 0 // For all extruders
#define DISABLE_X false
#define DISABLE_Y false
#define DISABLE_Z false
#define DISABLE_E false // For all extruders
#define DISABLE_INACTIVE_EXTRUDER true // Keep only the active extruder enabled.
#define INVERT_X_DIR true
#define INVERT_Y_DIR false
#define INVERT_Z_DIR true //CHANGED
#define INVERT_E0_DIR false
#define INVERT_E1_DIR false
#define INVERT_E2_DIR false
#define INVERT_E3_DIR false
#define INVERT_E4_DIR false
#define X_HOME_DIR -1
#define Y_HOME_DIR -1
#define Z_HOME_DIR -1
#define X_BED_SIZE 307 //CHANGED
#define Y_BED_SIZE 231 //CHANGED
#define X_MIN_POS 0 //CHANGED from 0
#define Y_MIN_POS 0 //CHANGED from 0
#define Z_MIN_POS 0 //CHANGED from 0
#define X_MAX_POS X_BED_SIZE
#define Y_MAX_POS Y_BED_SIZE
#define Z_MAX_POS 334 //CHANGED from 200
#define MIN_SOFTWARE_ENDSTOPS
  #define MIN_SOFTWARE_ENDSTOP_X
  #define MIN_SOFTWARE_ENDSTOP_Y
  #define MIN_SOFTWARE_ENDSTOP_Z
#define MAX_SOFTWARE_ENDSTOPS
  #define MAX_SOFTWARE_ENDSTOP_X
  #define MAX_SOFTWARE_ENDSTOP_Y
  #define MAX_SOFTWARE_ENDSTOP_Z
#define FILAMENT_RUNOUT_SENSOR //CHANGED uncommented
  #define NUM_RUNOUT_SENSORS   1     // Number of sensors, up to one per extruder. Define a FIL_RUNOUT#_PIN for each.
  #define FIL_RUNOUT_INVERTING true // set to true to invert the logic of the sensor. CHANGED to true from false
  #define FIL_RUNOUT_PULLUP          // Use internal pullup for filament runout pins.
  #define FILAMENT_RUNOUT_SCRIPT "M300 S5000\n  G91\n  M300 S5000\n  G1 Z+10\n  M300 S5000\n  G90\n  M300 S5000\n  G1 X0 Y0\n  M300 S5000\n  M104 S0\n  M300 S5000\n  M0" //CHANGED to M0 from M600
#define HOMING_FEEDRATE_XY (10*60) //CHANGED was 50*60
#define HOMING_FEEDRATE_Z  (1*60)
#define EEPROM_SETTINGS // Enable for M500 and M501 commands
#define EEPROM_CHITCHAT   // Give feedback on EEPROM commands. Disable to save PROGMEM.
#define HOST_KEEPALIVE_FEATURE        // Disable this if your host doesn't like keepalive messages
#define DEFAULT_KEEPALIVE_INTERVAL 2  // Number of seconds between "busy" messages. Set with M113.
#define BUSY_WHILE_HEATING            // Some hosts require "busy" messages even during heating
#define PREHEAT_1_TEMP_HOTEND 180
#define PREHEAT_1_TEMP_BED     70
#define PREHEAT_1_FAN_SPEED     0 // Value from 0 to 255
#define PREHEAT_2_TEMP_HOTEND 240
#define PREHEAT_2_TEMP_BED    110
#define PREHEAT_2_FAN_SPEED     0 // Value from 0 to 255
#define PRINTJOB_TIMER_AUTOSTART
#define LCD_LANGUAGE en
#define DISPLAY_CHARSET_HD44780 JAPANESE
#define SDSUPPORT
#define INDIVIDUAL_AXIS_HOMING_MENU //CHANGED uncommented
#define REPRAP_DISCOUNT_FULL_GRAPHIC_SMART_CONTROLLER
#define SOFT_PWM_SCALE 0
#define SERVO_DELAY { 300 }

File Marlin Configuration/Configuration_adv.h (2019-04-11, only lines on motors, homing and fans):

#define E0_AUTO_FAN_PIN -1
#define E1_AUTO_FAN_PIN -1
#define E2_AUTO_FAN_PIN -1
#define E3_AUTO_FAN_PIN -1
#define E4_AUTO_FAN_PIN -1
#define CHAMBER_AUTO_FAN_PIN -1
#define X_HOME_BUMP_MM 5
#define Y_HOME_BUMP_MM 5
#define Z_HOME_BUMP_MM 2
#define HOMING_BUMP_DIVISOR { 2, 2, 4 }  // Re-Bump Speed Divisor (Divides the Homing Feedrate)
#define MICROSTEP_MODES { 16, 16, 16, 16, 16 } // [1,2,4,8,16]
#define DIGIPOT_I2C_MOTOR_CURRENTS { 1.0, 1.0, 1.0, 1.0, 1.0, 1.0, 1.0, 1.0 }  //  AZTEEG_X3_PRO

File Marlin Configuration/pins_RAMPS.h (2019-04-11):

/**
 * Marlin 3D Printer Firmware
 * Copyright (C) 2016 MarlinFirmware [https://github.com/MarlinFirmware/Marlin]
 *
 * Based on Sprinter and grbl.
 * Copyright (C) 2011 Camiel Gubbels / Erik van der Zalm
 *
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
 */

/**
 * Arduino Mega with RAMPS v1.4 (or v1.3) pin assignments
 *
 * Applies to the following boards:
 *
 *  RAMPS_14_EFB (Hotend, Fan, Bed)
 *  RAMPS_14_EEB (Hotend0, Hotend1, Bed)
 *  RAMPS_14_EFF (Hotend, Fan0, Fan1)
 *  RAMPS_14_EEF (Hotend0, Hotend1, Fan)
 *  RAMPS_14_SF  (Spindle, Controller Fan)
 *
 *  RAMPS_13_EFB (Hotend, Fan, Bed)
 *  RAMPS_13_EEB (Hotend0, Hotend1, Bed)
 *  RAMPS_13_EFF (Hotend, Fan0, Fan1)
 *  RAMPS_13_EEF (Hotend0, Hotend1, Fan)
 *  RAMPS_13_SF  (Spindle, Controller Fan)
 *
 *  Other pins_MYBOARD.h files may override these defaults
 *
 *  Differences between
 *  RAMPS_13 | RAMPS_14
 *         7 | 11
 */

#if !defined(__AVR_ATmega1280__) && !defined(__AVR_ATmega2560__)
  #error "Oops!  Make sure you have 'Arduino Mega' selected from the 'Tools -> Boards' menu."
#endif

#ifndef BOARD_NAME
  #define BOARD_NAME "RAMPS 1.4"
#endif

//
// Servos
//
#ifdef IS_RAMPS_13
  #define SERVO0_PIN        7   // RAMPS_13 // Will conflict with BTN_EN2 on LCD_I2C_VIKI
#else
  #define SERVO0_PIN       11
#endif
#define SERVO1_PIN          6
#define SERVO2_PIN          5
#ifndef SERVO3_PIN
  #define SERVO3_PIN        4
#endif

//
// Limit Switches
//
#define X_MIN_PIN           3
#ifndef X_MAX_PIN
  #define X_MAX_PIN         2
#endif
#define Y_MIN_PIN          14
#define Y_MAX_PIN          15
#define Z_MIN_PIN          18
//#define Z_MAX_PIN          19

//
// Z Probe (when not Z_MIN_PIN)
//
#ifndef Z_MIN_PROBE_PIN
  #define Z_MIN_PROBE_PIN  32
#endif

//
// Steppers
//
#define X_STEP_PIN         54
#define X_DIR_PIN          55
#define X_ENABLE_PIN       38
#ifndef X_CS_PIN
  #define X_CS_PIN         53
#endif

#define Y_STEP_PIN         60
#define Y_DIR_PIN          61
#define Y_ENABLE_PIN       56
#ifndef Y_CS_PIN
  #define Y_CS_PIN         49
#endif

#define Z_STEP_PIN         46
#define Z_DIR_PIN          48
#define Z_ENABLE_PIN       62
#ifndef Z_CS_PIN
  #define Z_CS_PIN         40
#endif

#define E0_STEP_PIN        26
#define E0_DIR_PIN         28
#define E0_ENABLE_PIN      24
#ifndef E0_CS_PIN
  #define E0_CS_PIN        42
#endif

#define E1_STEP_PIN        36
#define E1_DIR_PIN         34
#define E1_ENABLE_PIN      30
#ifndef E1_CS_PIN
  #define E1_CS_PIN        44
#endif

/**
 * Default pins for TMC software SPI
 */
#if ENABLED(TMC_USE_SW_SPI)
  #ifndef TMC_SW_MOSI
    #define TMC_SW_MOSI    66
  #endif
  #ifndef TMC_SW_MISO
    #define TMC_SW_MISO    44
  #endif
  #ifndef TMC_SW_SCK
    #define TMC_SW_SCK     64
  #endif
#endif

#if HAS_DRIVER(TMC2208)
  /**
   * TMC2208 stepper drivers
   *
   * Hardware serial communication ports.
   * If undefined software serial is used according to the pins below
   */
  //#define X_HARDWARE_SERIAL  Serial1
  //#define X2_HARDWARE_SERIAL Serial1
  //#define Y_HARDWARE_SERIAL  Serial1
  //#define Y2_HARDWARE_SERIAL Serial1
  //#define Z_HARDWARE_SERIAL  Serial1
  //#define Z2_HARDWARE_SERIAL Serial1
  //#define E0_HARDWARE_SERIAL Serial1
  //#define E1_HARDWARE_SERIAL Serial1
  //#define E2_HARDWARE_SERIAL Serial1
  //#define E3_HARDWARE_SERIAL Serial1
  //#define E4_HARDWARE_SERIAL Serial1

  /**
   * Software serial
   */

  #define X_SERIAL_TX_PIN    40
  #define X_SERIAL_RX_PIN    63
  #define X2_SERIAL_TX_PIN   -1
  #define X2_SERIAL_RX_PIN   -1

  #define Y_SERIAL_TX_PIN    59
  #define Y_SERIAL_RX_PIN    64
  #define Y2_SERIAL_TX_PIN   -1
  #define Y2_SERIAL_RX_PIN   -1

  #define Z_SERIAL_TX_PIN    42
  #define Z_SERIAL_RX_PIN    65
  #define Z2_SERIAL_TX_PIN   -1
  #define Z2_SERIAL_RX_PIN   -1

  #define E0_SERIAL_TX_PIN   44
  #define E0_SERIAL_RX_PIN   66
  #define E1_SERIAL_TX_PIN   -1
  #define E1_SERIAL_RX_PIN   -1
  #define E2_SERIAL_TX_PIN   -1
  #define E2_SERIAL_RX_PIN   -1
  #define E3_SERIAL_TX_PIN   -1
  #define E3_SERIAL_RX_PIN   -1
  #define E4_SERIAL_TX_PIN   -1
  #define E4_SERIAL_RX_PIN   -1
#endif

//
// Temperature Sensors
//
#define TEMP_0_PIN         13   // Analog Input
#define TEMP_1_PIN         15   // Analog Input
#define TEMP_BED_PIN       14   // Analog Input

// SPI for Max6675 or Max31855 Thermocouple
#if DISABLED(SDSUPPORT)
  #define MAX6675_SS       66   // Do not use pin 53 if there is even the remote possibility of using Display/SD card
#else
  #define MAX6675_SS       66   // Do not use pin 49 as this is tied to the switch inside the SD card socket to detect if there is an SD card present
#endif
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

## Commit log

2019-04-11 Added Marlin configuration files
    Added edited Marlin configuration files
    [Configuration.h, Configuration_adv.h]
2019-04-11 Add Marlin Configuration Files directory and update README
    [Configuration.h, Configuration_adv.h]
2019-04-11 Added STL files
    [12mm Steel Rod Clamp V2.1.stl, 12mm Steel Rod Clamp V2.2.stl, 12mm Steel Rod Clamp V2.3.stl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]
2019-04-11 Added Fusion 360 Drawings and Model files
    [12mm Rod Clamp v19.f3d, 3_8 inch X-axis Bushing Holder v22.f3d, Acrylic Panel Clamp v16.f3d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]
2019-04-13 Created MODIFICATIONS.txt
    Created MODIFICATIONS.txt to show the changes to the configuration files and also how to install Marlin
2019-04-13 Added GNU GPL license to the Marlin configuration files
    Added GNU GPL license to the Marlin configuration files and changed the main LICENSE to note the exception.
    [Configuration.h, Configuration_adv.h]
2019-04-13 Changed STL Files
    [12mm Steel Rod Clamp V2.1.stl, 12mm Steel Rod Clamp V2.2.stl, 12mm Steel Rod Clamp V2.3.stl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]
2019-04-13 Add and remove more files
    [Log Book-Log.csv, Log Book-Statistics.csv, Parts Designed (All Versions).csv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]
2019-04-13 Remove two files
    [Printed Parts 123.csv, Tools 123.csv]
2019-04-13 Add files Parts and tools
    [Printed Parts.csv, Tools.csv]
2019-04-13 Removed Fusion 360 folders
    [12mm Rod Clamp v19.f3d, 3_8 inch X-axis Bushing Holder v22.f3d, Acrylic Panel Clamp v16.f3d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]
2019-04-13 Add Tools.pdf and Printed Parts.pdf, remove and replace STL files with latest version
    Add Tools.pdf and Printed Parts.pdf, remove and replace Hotend carriage STL files with latest version
    [Carriage Main V2.0.stl, Hotend Clamp Top V1.stl, Hotend Mount Plate V2.stl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]
2019-04-13 Created BOM.pdf
    Created Bill of Materials (BOM.pdf)
2019-04-14 Add to Wiring section
2019-04-14 Added Schematic.svg
2019-04-14 Changed and updated Schematic.svg (now Wiring.svg)
2019-04-14 Updated Wiring.svg
2019-04-14 Added wiring pictures
2019-04-14 Add switch wiring pictures
2019-04-14 Updated switch wiring pictures
2019-04-15 Begin work on Assembly section
2019-04-15 Add to Assembly: Step 1
2019-04-15 Work on Step 2 of the Assembly section
2019-04-15 Add Spliced and Splicing wires
2019-04-15 Add pictures and text to IKEA Lack Tables in Assembly section
2019-04-15 Add pictures for PVC Pipe Clamp and PVC Pipe Joiner
2019-04-17 Add pictures of acrylic spacers and hinges
2019-04-18 Add to acrylic toggle and panel clamps section
2019-05-13 Add pictures for Acrylic Panel Clamp
2019-05-13 Work on Panel Clamp section

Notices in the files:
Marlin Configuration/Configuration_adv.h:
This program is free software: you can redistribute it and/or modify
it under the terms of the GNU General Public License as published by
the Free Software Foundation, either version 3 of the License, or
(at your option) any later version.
